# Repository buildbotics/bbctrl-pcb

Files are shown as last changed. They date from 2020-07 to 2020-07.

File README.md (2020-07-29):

# Buildbotics Controller Schematics & PCB Layout
The top-level schematic is in the file ``buildbotics_controller.sch``.  To view
and edit the schematics run:

    make schematics

You must have ``make`` and the GEDA tools install.  Other make commands are:

  * ``pcb``    - Open the PCB editor.
  * ``bom``    - Create Bill of Materials as ``buildbotics_controller.bom``.
  * ``net``    - Generate the netlist as ``buildbotics_controller.net``.
  * ``drc``    - Run the Design Rule Checker.
  * ``layout`` - Initialize the PCB layout.
  * ``attrib`` - Edit schematic part attributes.
  * ``zip``    - Create a zip file from the Gerber and drill files.
  * ``tidy``   - Remove all backup files.
  * ``clean``  - Remove all autogenerated files.

# Configuration notes
Copy the system gnetlistrc file:

    mkdir -p ~/.gEDA
    cp /etc/gEDA/system-gnetlistrc ~/.gEDA/gnetlistrc

Edit ``~/.gEDA/gnetlistrc`` and comment out (insert semicolon) the line that
reads:

    (hierarchy-netattrib-mangle "enabled")

and uncomment the line that reads:

    ;(hierarchy-netattrib-mangle "disabled")

The resulting lines should look like this:

    ;(hierarchy-netattrib-mangle "enabled")
    (hierarchy-netattrib-mangle "disabled")

This allows power and ground rails to be routed between schematics without
mangling the names.  Note, that as a consequence of this setting you cannot
use ``net`` attributes in any schematic modules that are used more than once
with out having them all connected together.

Set the library path in PCB to point to the local footprints folder.  Use
``File->Preferences->Library`` in PCB to do this.

# License
Copyright Buildbotics LLC 2016-2020.

This source describes Open Hardware and is licensed under the CERN-OHL-S v2

You may redistribute and modify this documentation and make products
using it under the terms of the CERN-OHL-S v2 (https:/cern.ch/cern-ohl).
This documentation is distributed WITHOUT ANY EXPRESS OR IMPLIED
WARRANTY, INCLUDING OF MERCHANTABILITY, SATISFACTORY QUALITY
AND FITNESS FOR A PARTICULAR PURPOSE. Please see the CERN-OHL-S v2
for applicable conditions.

Source location: https://github.com/buildbotics

As per CERN-OHL-S v2 section 4, should You produce hardware based on
these sources, You must maintain the Source Location clearly visible on
the external case of the CNC Controller or other product you make using
this documentation.

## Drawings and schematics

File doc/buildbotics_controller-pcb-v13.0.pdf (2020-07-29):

## buildbotics_controller.pcb

## 1. Table of Contents (This Page) Created on Wed Jul 29 16:05:18 2020 2. top 3. power 4. ground 5. bottom 6. plated-drill 7. unplated-drill 8. componentmask 9. soldermask 10. topsilk 11. bottomsilk 12. toppaste 13. topassembly 14. bottomassembly 15. fab

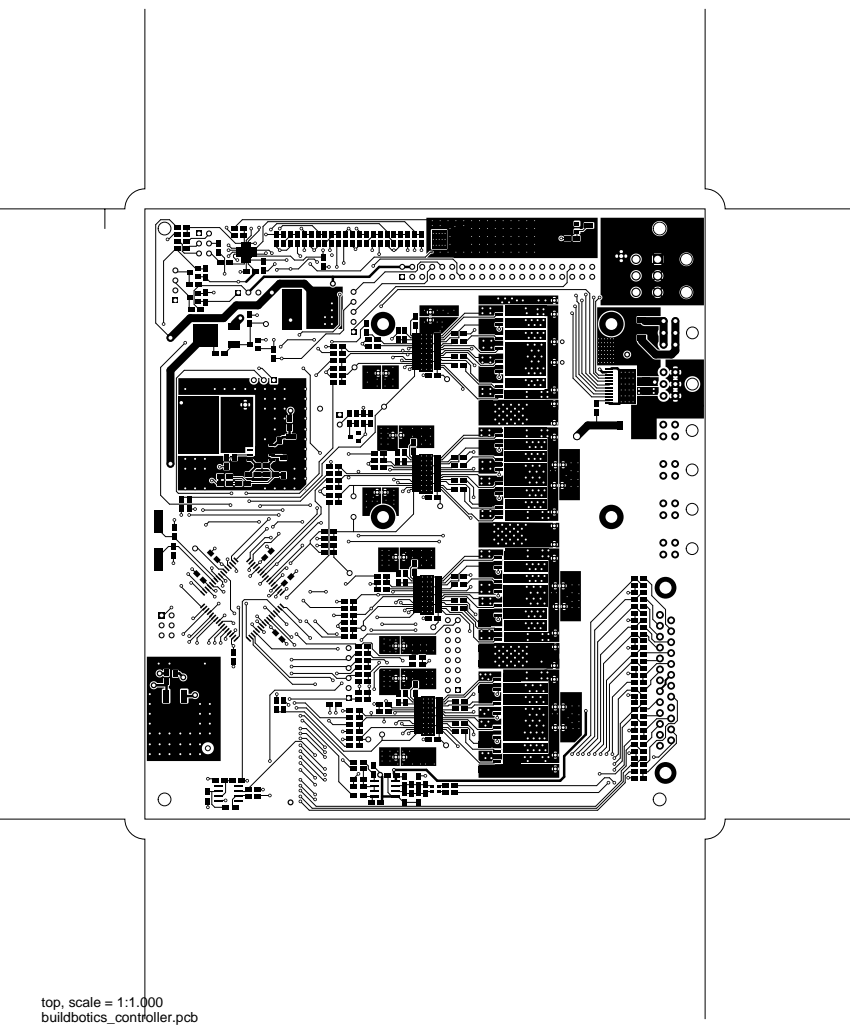
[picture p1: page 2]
top, scale = 1:1.000

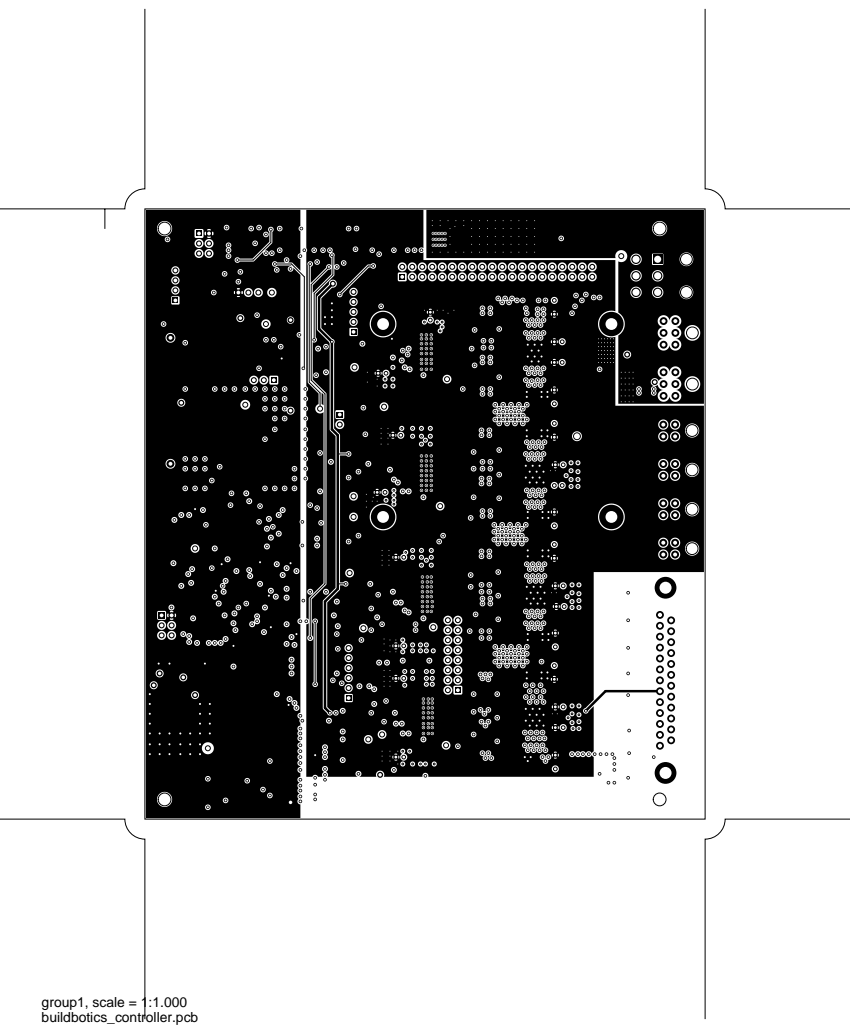
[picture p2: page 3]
group1, scale = 1:1.000

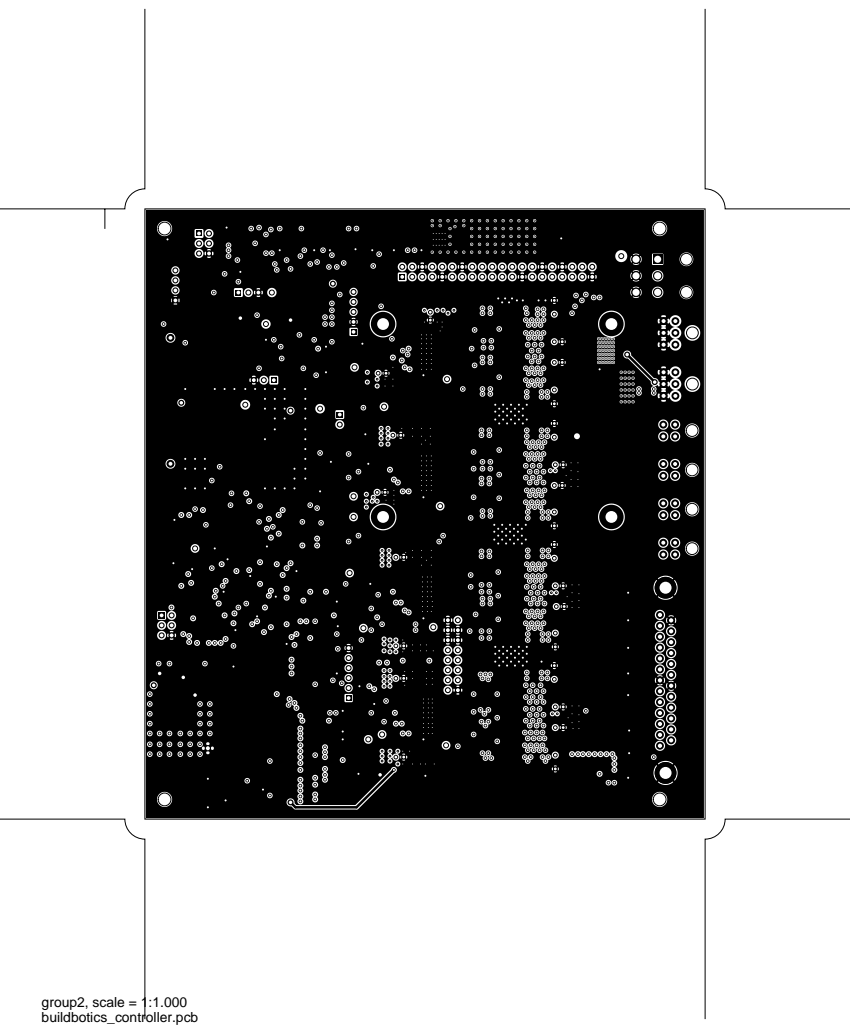
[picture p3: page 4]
group2, scale = 1:1.000

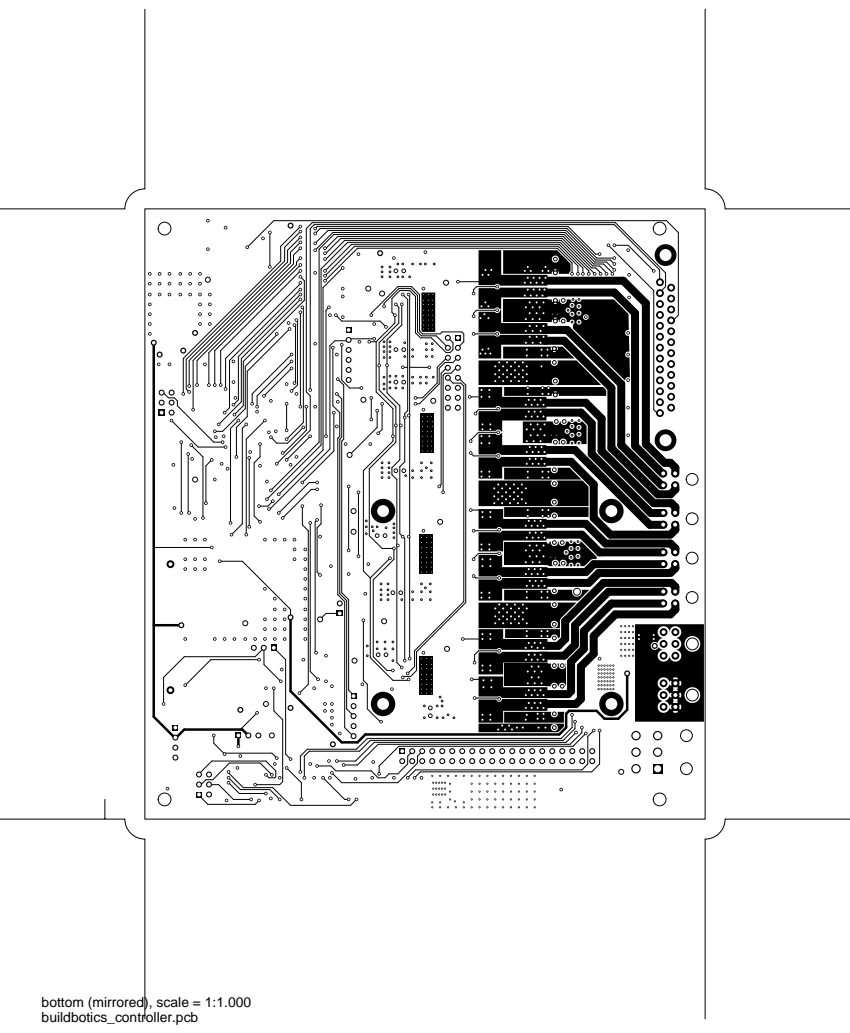
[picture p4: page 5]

bottom (mirrored), scale = 1:1.000

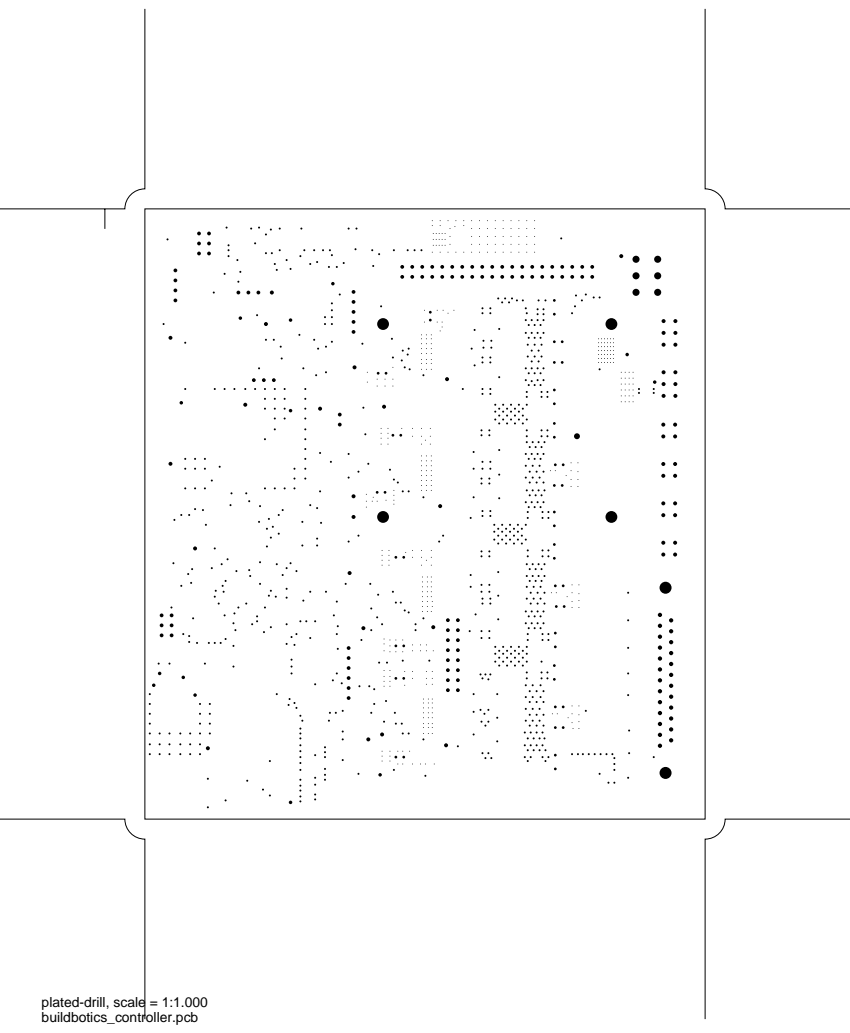
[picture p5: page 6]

plated-drill, scale = 1:1.000

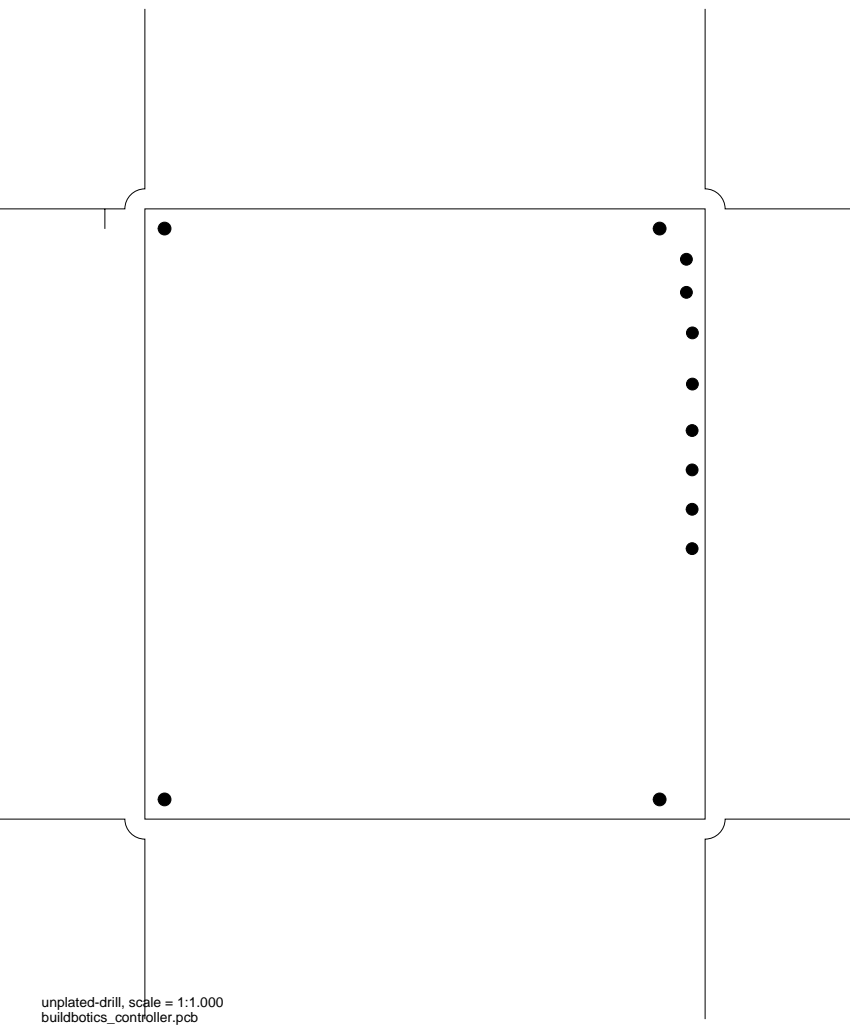
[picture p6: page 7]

unplated-drill, scale = 1:1.000

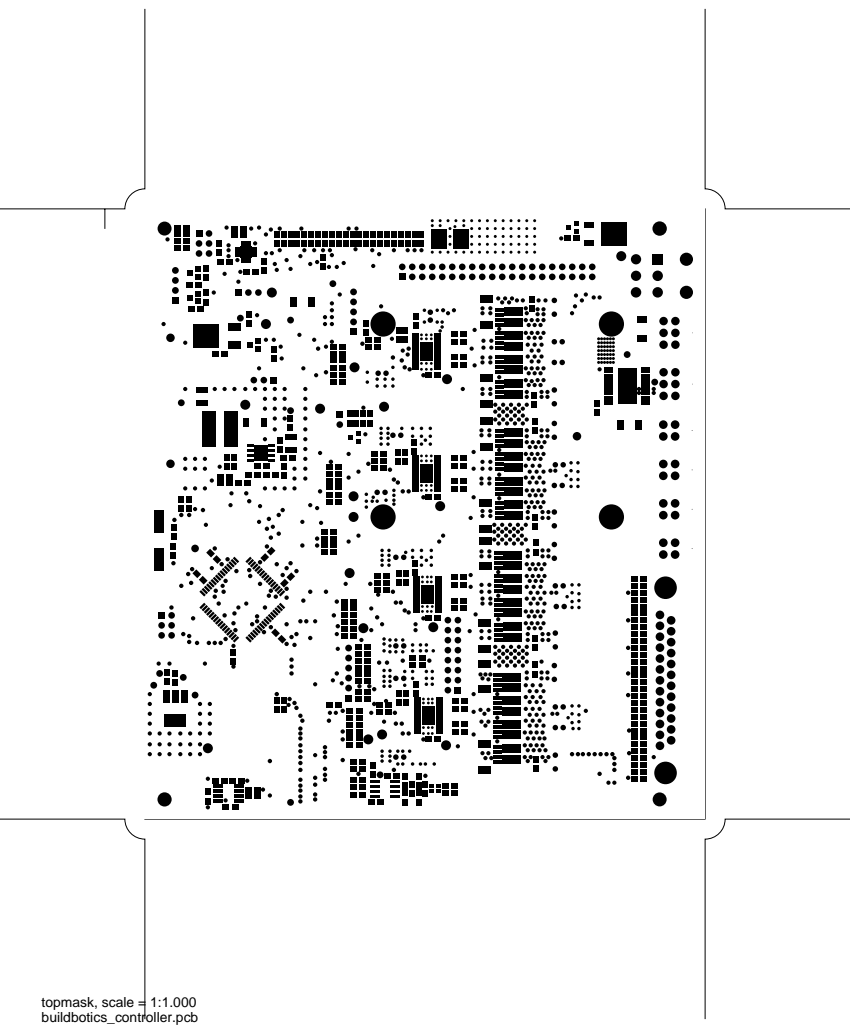
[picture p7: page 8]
topmask, scale = 1:1.000

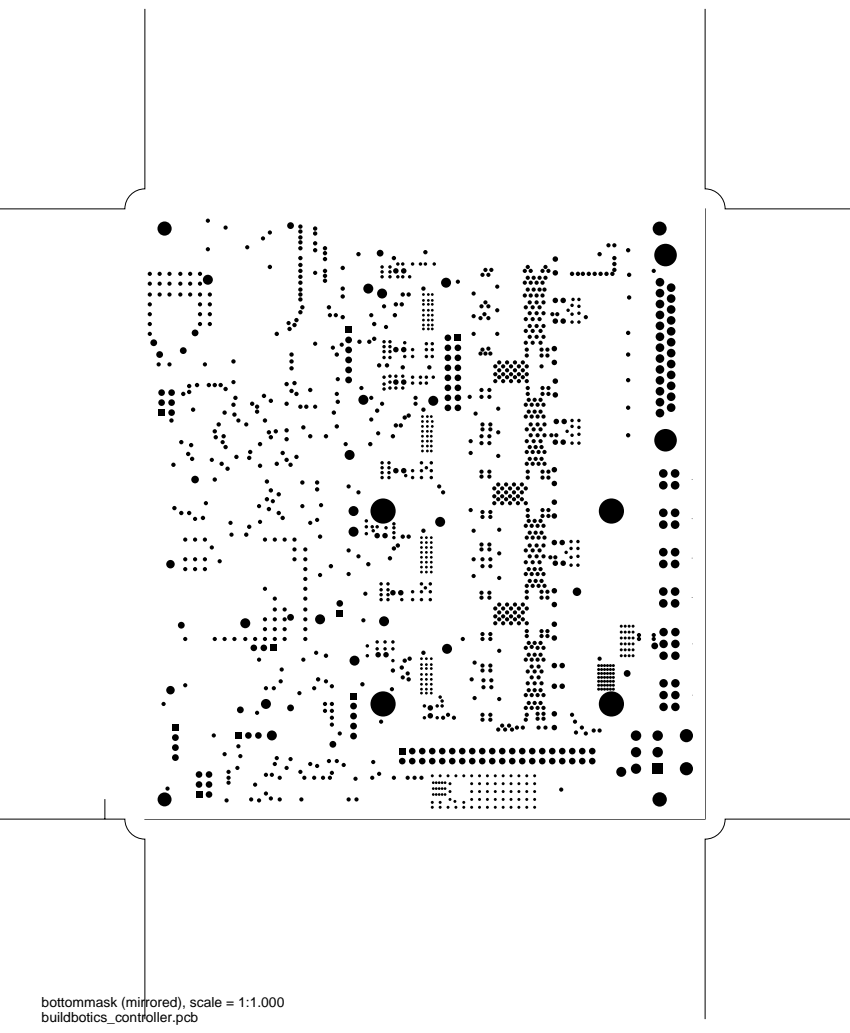
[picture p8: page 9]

bottommask (mirrored), scale = 1:1.000

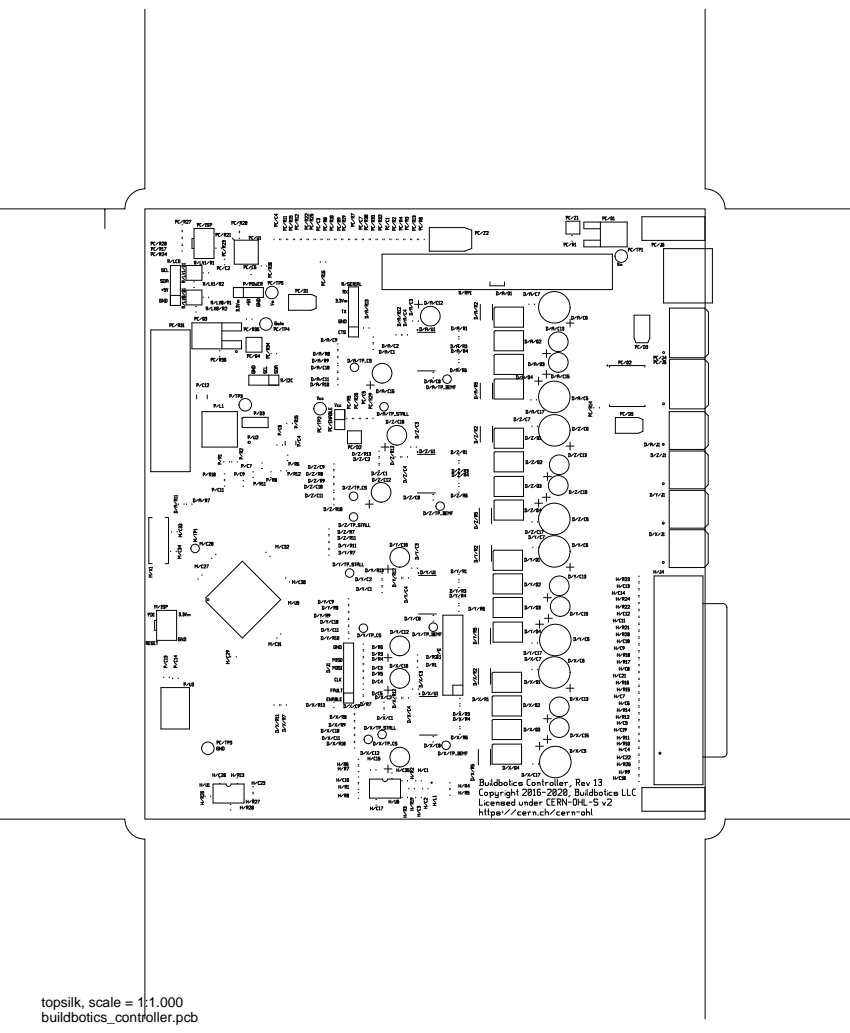
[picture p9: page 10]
topsilk, scale = 1:1.000

bottomsilk (mirrored), scale = 1:1.000

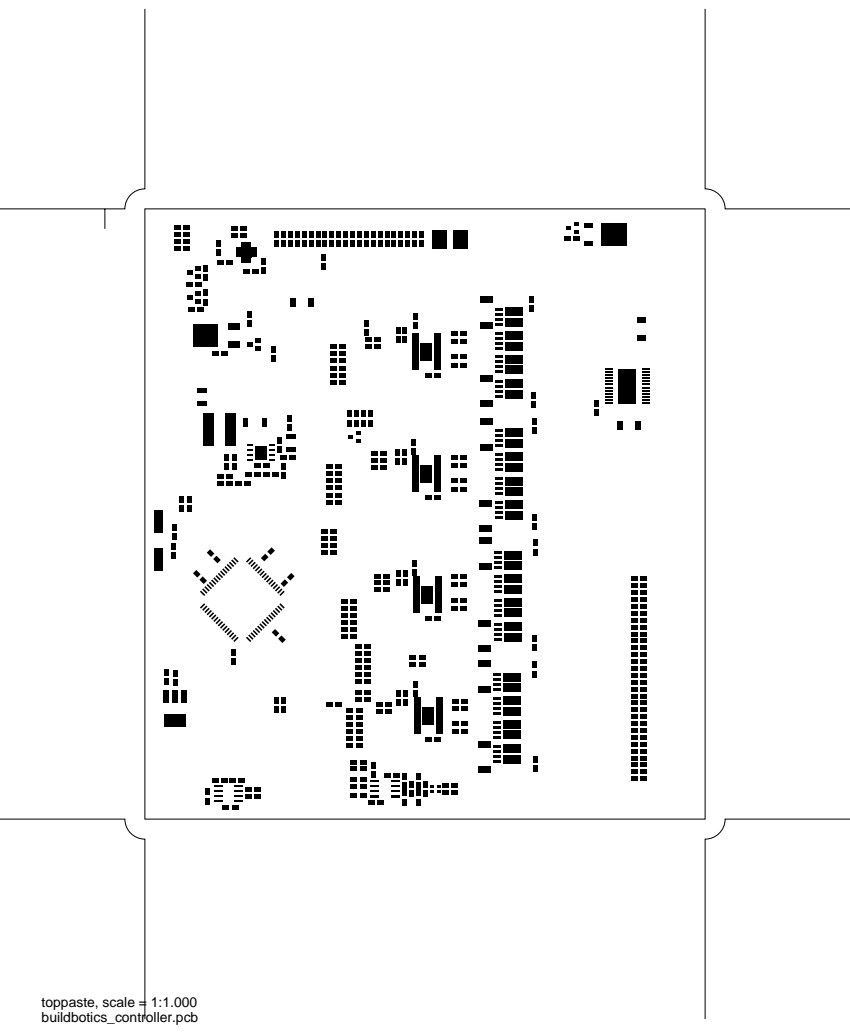
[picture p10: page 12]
toppaste, scale = 1:1.000

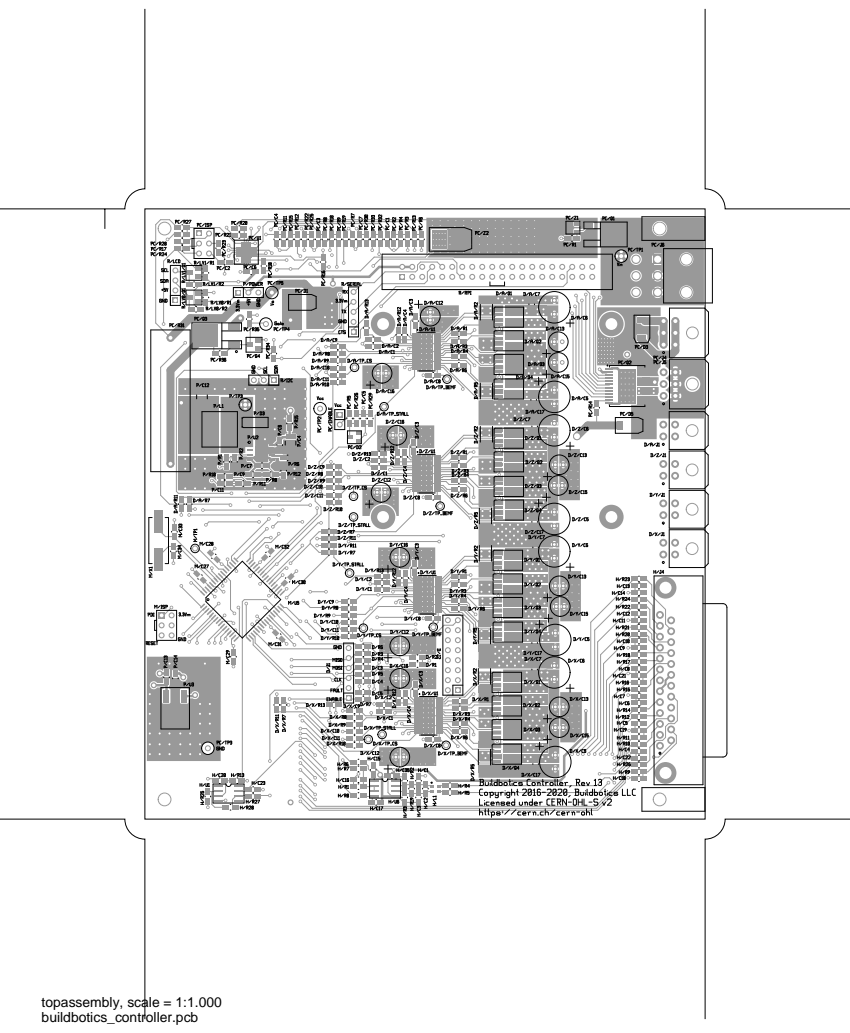
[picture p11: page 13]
topassembly, scale = 1:1.000

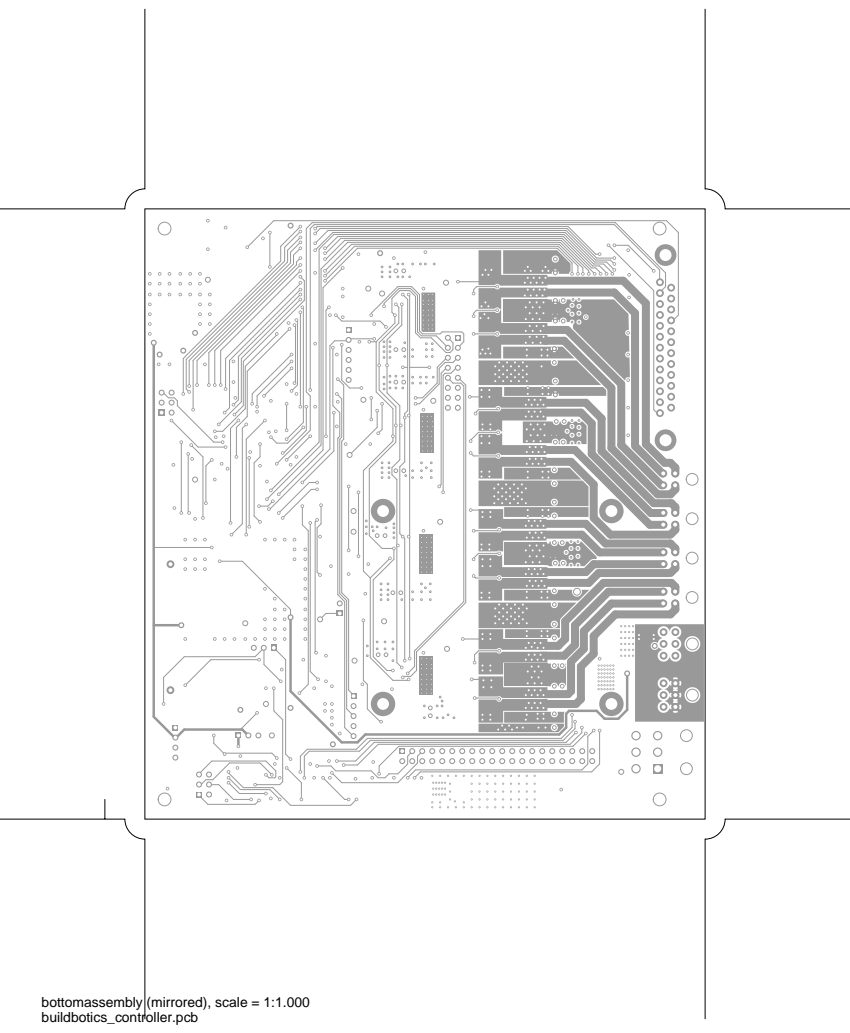
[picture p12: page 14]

bottomassembly (mirrored), scale = 1:1.000

fab, scale = 1:1.000

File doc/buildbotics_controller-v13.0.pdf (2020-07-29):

PAGE; DRAWN BY:

Level Converter
Copyright (c) 2016−2020, Buildbotics LLC
Licensed under CERN−OHL−S v2

Doug & Joe Coffland


NC NCMicroprocessor Copyright (c) 2016−2020, Buildbotics LLC

Licensed under CERN−OHL−S v2


Peripherals
Copyright (c) 2016−2020, Buildbotics LLC
Licensed under CERN−OHL−S v2


2 G1 | | | D1 | 7
3 S2 | D2 | 6
4 G2 | | | D2 | 5

Motor Driver
Copyright (c) 2016−2020, Buildbotics LLC
Licensed under CERN−OHL−S v2

PAGE; DRAWN BY:; Raspberry PI

Stepper Motor Drivers

Buildbotics Controller
Copyright (c) 2016−2020, Buildbotics LLC
Licensed under CERN−OHL−S v2

Doug & Joe Coffland


Power
Copyright (c) 2016−2020, Buildbotics LLC
Licensed under CERN−OHL−S v2

PAGE; DRAWN BY:

NC NC NC NC NC NC serial_tx:1 serial_rx:1 serial_cts:1

RPI Bus
Copyright (c) 2016−2020, Buildbotics LLC
Licensed under CERN−OHL−S v2

Doug & Joe Coffland


Power Conditioning
Copyright (c) 2016-2020, Buildbotics LLC
Licensed under CERN-OHL-S v2


Motor Modules
Copyright (c) 2016−2020, Buildbotics LLC
Licensed under CERN−OHL−S v2

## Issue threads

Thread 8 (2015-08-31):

Supply motor logic from motor driver 5-volt supply

DougCoffland, 2015-08-31:
a. We could avoid the second IRM-10-5 by using the 5v supply on the
TMC2660.  These could all just be ganged together.  Saves ~$7.50.

DougCoffland, 2018-02-13:
No longer desired.

Closed 2018-02-13.

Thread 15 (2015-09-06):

Consider copper filling/pouring in the ground plane

jcoffland, 2015-09-06:
Isn't it generally a good idea to copper fill the ground plane?  You've done this already for the motor ground but why not also do so for the logic ground plane?  I was able to do this by drawing a few polygons on layer `inner 2` so that they did not overlap the motor ground plane.  I didn't check this in though.  What do you think?

sntanala, 2019-06-09:
Hi jcoffland, my name is Satya, I am a learner and programmer for cnc controller, can you please let us know how can i open eagle schematics of this project, I tried all versions of eagle but we are getting error while open. can you please suggest me how to open these schematics to learn control flows.

Closed 2019-06-09.

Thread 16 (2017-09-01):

Schematic PDF

DirtyEngineer, 2017-09-01:
Including a PDF of the schematic would be great.

jcoffland, 2017-09-01:
Good idea: https://github.com/buildbotics/bbctrl-pcb/blob/master/doc/buildbotics_controller-v8.1.pdf

Closed 2017-09-01.

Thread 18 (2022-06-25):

Can we get a Kikad version of this?

ArcAIN6, 2022-06-25:
I was wondering if there were alternative formats for these schematics / PCB files? gEDA seems to be very antiquated, and not windows friendly at all. As i don't have a linux machine here, i tried to open these on raspberry pi, following the install directions on teh gEDA website, but the schematics won't show up, and the PCB viewer is  completely non-functional.

Any help would be great, as i'm interested in how these boards work

leventelist, 2023-11-01:
Yes please.

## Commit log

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2015-08-05 Reworked power, cleaned up symbols
    [connectors.sch, io_board.sch, io_bus.sch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]
2015-08-06 made schematic changes, started a new static file, added flag symbol, and added datasheet for nucleo
    [PowerSTEP01 board2.sch]
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2015-08-11 replacediodes on board because part is not available. New diodes are CDBU0130L
    [BOM.ods, PowerSTEP01 board.sch, PowerSTEP01 board2.sch]
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2015-08-12 corrected a few parts and created bill of materials (BOM.ods)
    [BOM.ods, PowerSTEP01 board.sch, PowerSTEP01 board2.sch]
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2015-08-22 fixed clock lines by adding clock.sch schematic ad symbol and modified isolation.sch accordingly
    [BOM.ods, clock.sch, isolation.sch]
2015-08-25 completed combined board layout. Still have warnings and one being reported as not routing. Will continue to investigate
    [BOM.ods, isolation.sch, microprocessor.sch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]
2015-08-25 I fixed the warnings but there gpcb still reports that one rat is not routed, even though it is not apparent from looking at the board. I also cut the board down to it's final size which is 85mm x 22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
2015-08-26 All warnings anre now cleared and all rats have been routed. In addition, BOM has been created (see BOM.ods) and gerbers are presnt
    [BOM.ods, motor_driver.sch, rpi_bus.sch]
2015-08-29 This is a major rework. I changed board size to 5 X 8 inches and 4 layers. I also added the 26-Pin DSub connector for the IO connector. I also reduced the number of drivers to four. I added mounting 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
    [BOM.ods, clock.sch, combined.sch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]
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2015-08-30 Corrected some errors so it now passes BayArea Circuits DFM tool and corrected a bunch of local DRC errors. Still working on correcting DRC errors.
2015-08-30 corrected hole size for 26 pin dsub foot print and corrected all DRC errors below 6 mils
2015-08-30 Corrected foot print for 260 mil cap and 8 by 10 cap - All DRC errors below 7.5 mils are now correct. Still get a warning however that a hole is too close to a line.
2015-08-30 corrected footprint for 2-pin Molex. All DRC below 7.5mil corrected and no warning about hole too close to line.
2015-08-31 All DRC errors cleared. No errors or warnings using Advanced Circuits FreeDFM tool.
    [microprocessor.sch, motor_driver.sch]
2015-08-31 dir_4 and step_4 were swapped on the schematic and therefore swapped ont the layout. The schematic and layout have been corrected.
    [motor_module.sch]
2015-09-01 Corrected pin swap of serial_rx and serial_tx and fixed missing refdes on RPI connector
    [combined.sch, microprocessor.sch, rpi_bus.sch]
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2015-09-03 New board with corrected connectors, removal of extra IRM-10-5, replacement of digital isolators withoptos, etc... No DRC errors, not errors or warnings at Advanced Circuits DFM. This board is marked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
    [BOM.ods, clock.sch, isolation.sch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]
2015-09-04 moved clock oscillator on board reducing total clock line length from 8 inches to 3 inches
2015-09-04 cleared all DFM errors and created BOM
2015-09-05 corrected footprint size for PS1/C1
    [power.sch]
2015-09-05 corrected raspberry pi connector and board footprint, added outline to layout, corrected footprint on PS1/C1, started working on final BOM file
    [BOM.ods, rpi_bus.sch]
2015-09-05 corrected soldermask line width around raspberry_pi mounting holes
2015-09-06 scrubbed BOM and created ASSY_BOM.xlsx for assy estimate, corrected footprint for PS1/C4, made land pattern for OSC match datasheet land pattern, assigned part numbers to MP1/C2 and C3 and corrected 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
    [BOM.ods, microprocessor.sch, power.sch]
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2015-09-06 corrected land pattern for C17 on the Motor Drivers
2015-09-06 Corrected connection to 5VOUT on motor drivers, updated layout, expanded ground plane on layout
    [motor_driver.sch]
2015-09-06 io labels in microprocessor.sch corrected
    [microprocessor.sch]
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2015-09-08 corrected pin order on PS1/J2 footprint and then fixed layout accordingly
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2015-09-10 replaced 0201 caps on microprocessor.sch with 0402s to lower assembly cost; affected combined.pcb, BOM.pcb, and ASSY_BOM.xlsx
    [BOM.ods, microprocessor.sch]
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2015-09-11 reviewed and verified all footprints, updated BOMs with new io connecton for e-stop, updated rpi_bus.sch with new connector circuit for e-stop, created BOMs and centroid files for thru hole and no th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
    [BOM.ods, rpi_bus.sch]
2015-09-27 added tabs to RPI/J1 and RPI/J2; confirmed no DFM errors on Advanced Circuits DFM tool
    [rpi_bus.sch]
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2015-11-30 added files describing back, bottom, and top of enclosure, and added logo file
    [backview.dxf, bottomplate.dxf, topcover.dxf]
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2016-02-04 Fixed net attributes
    [microprocessor.sch, motor_driver.sch, motor_module.sch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]
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2016-02-05 Fixed DRC errors
    [microprocessor.sch, motor_driver.sch, rpi_bus.sch]
2016-02-05 Shortened refdes, make changes, docs
    [buildbotics_controller.sch, motor_module.sch]
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2016-02-08 v2.0 close to done, finalized connectors, add some footprints, removed unused footprints
    [buildbotics_controller.sch, load.sch, microprocessor.sch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]
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2016-02-09 Fixed LED
    [peripherals.sch]
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2016-02-09 fixed name of kingbright footprint file
2016-02-09 fixed kingbright footprint again
2016-02-09 changed Power Supply J1 from 350944 (which is male) to 643230 (which is female) which now mates correctly with the male connector on the mean well GS280 power supply. Created footprint for 643230. Re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
    [power.sch]
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2016-02-10 fixed pin numbers on mosfet symboll for load/Q2
    [load.sch]
2016-02-10 fixed rpi footprint and added board outline to footprint. Updated rpi_bus.sch with correct footprint
    [rpi_bus.sch]
2016-02-11 corrected spelling on footprint name for LM5160
    [power.sch]
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2016-02-11 modified power.sch to make switch S1 into two tabs, assigned device Keystone 1212 to use a through hole tab, and made footprint for Keystone 1212 tab.
    [power.sch]
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2016-02-12 added part numbers for R11, R13, C23, C24 in motor_driver.sch. Added C25 and C26 across sense resistors as per section 8.1 of tms2660 datasheet.Continued to update layout in buildbotocs_controller.pcb
    [motor_driver.sch]
2016-02-12 fixed 3.3V_motor.sym to use net=3.3Vm:1 instead of net=+5Vm:1. Continued with layout and continued updating motor_driver.sch to reflect component model names
    [motor_driver.sch]
2016-02-15 continued to work on layout updating buildotics_controller.pcb; continued to identify specific parts in schematic and added part numbers and descriptions in load.sch, motor_driver.sch, peripherals.sc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
    [load.sch, motor_driver.sch, peripherals.sch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]
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2016-02-16 corrected value for P/C4 from 4.7uF to .47uF per 8.1.2.1.7 in the LM5160 datasheet, completed assigning part numbers in power.sch and motor_driver.sch; continued layout work
    [motor_driver.sch, power.sch]
2016-02-16 fixed footprint for LM5160 (no pin numbers were assigned; continued layout
    [power.sch]
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2016-02-18 PCB layout complete with no local DRC errors
    [rpi_bus.sch]
2016-02-18 fixed footprints to increase clearance to make DRC pass
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2016-02-19 layout complete, no DRC errors, Cleared all show stoppers from FreeDFM; Cleared many warnings from FreeDFM ( had to increase soldermask size on most of the footprints that I created. Reduced board wo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
    [microprocessor.sch]
2016-02-19 board layout complete with no local DRC errors and no errors or warnings from freeDFM. Note, also deleted unused raspberry_pi_board.fp footprint file
2016-02-20 assigned specific part numbers and values to each component in the schematics
    [load.sch, microprocessor.sch, motor_driver.sch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]
2016-02-20 started BOM; continued to specify exact part numbers in schematics; extended footprint on MAX14850 as requested by Mike; updated pcb layout accordingly
    [BBC_BOM.ods, motor_module.sch, power.sch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]
2016-02-20 completed bill of materials; changed ISP connector from right angle to vertical; added value field to some parts to make compatible with bill of materials output
    [BBC_BOM.ods, load.sch, microprocessor.sch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]
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2016-02-21 changed sense resistors from 1206s to 2512s; updated schematic,BOM, centroid file, and layout accordingly
    [motor_driver.sch]
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2016-02-26 Added reverse voltage protection
    [power.sch]
2016-02-28 changed board size to 152.3mm x 142.3mm and re-centered layout; Added mounting holes; removed R/LED1, R/R22, and R/R23; replaced fuse/diode polarity protection circuit with NMOSFET/diode/resistor pro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
    [power.sch]
2016-02-29 added footprint file for 2512 resistors, replaced P/D1 with part recommended by Joe, completed layout with no shorts, DRC errors, or FreeDFM errors
    [power.sch]
2016-02-29 Schematic cosmetic updates, changed LD#/J1 pinout, Fixed disconnect on rpi_sda
    [load.sch, power.sch, rpi_bus.sch]
2016-03-01 implemented all of Joes recommendations; NDRC errors; fully routed; added copyright, board name; and company name to silk screen
    [microprocessor.sch]
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2016-03-08 updated supporting parts list and made dxf files for front and back panel of enclosure
    [back_panel.dxf, front_panel.dxf]
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2016-06-03 Attempts to fix LM5160 circuit
    [load.sch, microprocessor.sch, peripherals.sch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]
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2016-06-15 added 1210 footprint with extended pads, referenced 1212_ext in power.sch, referenced 0805_ext in level_converter.sch
    [level_converter.sch, power.sch]
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2016-06-17 Rearranged AVR & DB25 pins, Moved reset line on isolator, Added grounds to motor test headers
    [microprocessor.sch, motor_driver.sch, peripherals.sch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]
2016-06-19 created footprints for C10, T1, Z2, and D2 in power.sch and referenced all parts in Isolated Flyback circuit schematic to models and footprints
    [power.sch]
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2016-06-19 changed 0805 footprints in load.sch to 0805_ext, created footprint for common mode choke in peripherals.sch and updated footprints and footprint references in peripherals.sch.
    [load.sch, peripherals.sch]
2016-06-19 corrected references to pin 2 in 0806_ext.fp and DO214AC.fp, fixed mounting hole in Molex_39-30---6-.fp, made mounting holes metal connection to pin 26 in NORCOMP_182-025-113R151_DB25M.fp, corrected 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
    [power.sch]
2016-06-20 corrected wiring on P/J1, fixed wiring on motor connectors, connected P/R1 to pwr_en so Vs is off when the switch is off
    [motor_driver.sch, power.sch]
2016-06-23 completed layout with no DRC, no shorts, and all nets routed, still need to submit to Advanced Circuits for DFM check, increased clearance on SRF2012A footprint, added new schottkyA2K1.sym symbol due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
    [load.sch]
2016-06-23 changed zener symbol to match footprint and updated power.sch, note this was done before the previous push but I for did not get these files included. Current status is layout is done, but still need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
    [power.sch]
2016-06-24 adjusted clearance on SRF2012A footprint, all DFM errors now cleared with Advanced Circuits
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2016-06-26 modified softstart circuit in power.sch, removed Zener in polarity control circuit, changed R20 to 100 ohms decreasing C1 charge time, reduced C20 to 1uF reducing Q1 turnon time, added D4 to provide 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
    [power.sch]
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2016-06-26 Fixed zener alignment, added new poposed power conditioning circuit.
    [power2.sch]
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2016-06-29 Fixed schematic DRC warings/errors, added caps to H/J4 input lines, Renamed peripherial module P->H to avoid conflicts with RPI module
    [buildbotics_controller.sch, peripherals.sch, power.sch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]
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2016-06-30 layout complete, not opens, shorts, DRC errors,or DFM errors. Changed Diode D1 in power.sch to get smaller footprint.
    [power.sch]
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2016-07-01 cleared all dfm errors and moved silkscreen labels around
2016-07-02 changed some part numbers because we were using different models for exactly the same part. This allows us to get larger volumes and fewer different parts
    [motor_driver.sch, peripherals.sch, power.sch]
2016-07-03 fixed a DRC error and corrected board width to 142.3mm
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2016-07-26 Added i2c bus from RPi to AVR, fixed some part numbers
    [microprocessor.sch, motor_driver.sch, peripherals.sch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]
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2016-07-28 Fixed PCB schematic path, Fixed bad MOSFET pin numbers
    [level_converter.sch, load.sch, power.sch]
2016-07-29 layout done, DRC and DFM errors cleared, fixed footprint for P/U5 because footprint did not match symbol, reversed power rails in P/U5 because the appeared to be connected backwards, changed foorprin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
    [power.sch]
2016-08-05 Check all PCB major parts, improved routing, fixed MOSFETs
    [level_converter.sch, load.sch, microprocessor.sch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]
2016-08-16 Split RPi footprint, Moved RPi mounting holes, Better noise immunity, Routing improvements.
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2016-08-18 fixed soldermask clearance on seveal vias
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2016-09-29 Fixed cap value
    [power.sch]
2016-10-09 Replaced TMC2660 with DRV8711, Added filtering to serial lines, Modified motor connector footprint pin numbers, Connected BEMF lines to AVR
    [microprocessor.sch, motor_driver.sch, motor_module.sch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]
2016-10-09 Added correct refdes to resistors
    [motor_module.sch, rpi_bus.sch]
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2016-10-09 Fixed schematic DRC violations
    [motor_driver.sch, rpi_bus.sch]
2016-10-10 added model numbers to C1 an C2 in rpi_bus.sch. The are caps that Joe added to the serial lines.
    [rpi_bus.sch]
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2016-10-10 replaced power conditioning circuit in power.schj
    [power.sch]
2016-10-10 corrected conflicting refdes's in power.sch
    [power.sch]
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2016-10-10 assigned component model numbers and descriptions as needed in motor_driver.sch and motor_module.sch
    [motor_driver.sch, motor_module.sch]
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2016-10-10 created footprint for DRV8711, added footprints for Nichicon 3mm cap and TO252. Updated references to new footprints in schematics. All footprints now load into pcb and I can start routing
    [motor_driver.sch, power.sch]
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2016-10-13 Fixed motor driver connections, shunk power supply symbols.
    [microprocessor.sch, motor_driver.sch, motor_module.sch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]
2016-10-14 Layout complete, no shorts, no opens, noDRC errors, no DFM errors from Advanced Circuits. Includes new L7986A layout and new place for 3-pin header for enable switch connection and new power supply c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
    [power.sch]
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2016-10-16 Added new power conditioning circuit, some PCB fixes
    [power.sch]
2016-10-16 assigned correct footprint to LM293DT in power.sch
    [power.sch]
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2016-10-19 assigned part numbers to power.sch, finished layout in buildbotics_controller.pcb, put in new power circuit, moved +5 iso, +5Vm, and +3.3Vm powersupplies around for better routing, moved digital isol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
    [power.sch]
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2016-10-20 new schematic reflects new dual mosfets with drain tabs, corrected routing of ASENSE test point line, it was going to the wrong place
    [motor_driver.sch]
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2016-10-21 Fixed cap values
    [peripherals.sch]
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2016-10-24 layout complete with no legitimate DRC errors, removed filter components on open collector lines in schematics, corrected connection of senseA lines in drivers
    [load.sch, motor_driver.sch, motor_module.sch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]
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2016-10-30 replaced power supply filter caps in motor_driver.sch with modeled components and added footprint files as needed
    [motor_driver.sch]
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2016-10-30 removed unnecessary resistors in gate drive lines in motor_driver.sch and in layout
    [motor_driver.sch]
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2016-10-31 replaced caps with values that Joe and I agreed upon
    [motor_driver.sch]
2016-10-31 removed and replaced caps on schematic and layout and added footprint for one electolytic"
    [motor_driver.sch]
2016-11-02 layout complete with no legitimate DRC errors, changed testpoints a bit in power.sch and rpi_bus.sch to make routing easier
    [power.sch, rpi_bus.sch]
2016-11-03 added capacitance pours to bottom layer, all DRC and DFM errors cleared
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2016-11-05 Moved all unlocked parts, lines and vias on to grid. Fixed via thermals. Lots of fixes to silk layer. Moved level shifters. Moved power cond. circuit. Added missing labels. Fixed R/SERIAL labels. Ali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
2016-11-05 Fixed connector positions and locked them
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2016-11-07 Increased clearance and thermal finger width
2016-11-12 corrected some part numbers
    [motor_driver.sch, power.sch]
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2016-11-23 fixed footprint for P/J1, improved footprint fo TSSOP38 by reducing solder mask clearance, moved non-ISO PS up, level shifters down, and power conditioning compomponents down a little to allow slidin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
    [power.sch]
2016-11-25 changed a couple of part numbers for equal valued comcomponents so we could get larger quantities of individual part numbers
    [level_converter.sch, power.sch]
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2017-01-04 fixed solder mask violations
2017-01-06 power_cond.sch and .pcb updated, mask clearance corrected in footprint file
    [power_cond.sch]
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2017-02-23 Fix grid alignment, moved power_cond3 -> power_cond
    [power_cond.sch, power_cond3.sch]
2017-02-26 latest power_cond sicruit with self protecting fet, also includes load circuit switches for testing
    [power_cond.sch]
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2017-02-27 corrected footprint for ATiny, started power_cond.pcb layout, corrected symbol for ATiny, added decoupling cap on ATiny in power_cond.sch and reconnected pin21 to gnd.
    [power_cond.sch]
2017-02-28 Power cond fixes & cleanup
    [power_cond.sch]
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2017-02-28 corrected footprint attribute for ISP and J3 in power_cond.sch, corrected footprint for ATiny, completed layout in power_cond.pcb
    [power_cond.sch]
2017-03-03 added diodes on outputs and added reverse battery battery circuit in parallel with zero ohm resistor in power_cond
    [power_cond.sch]
2017-03-07 created power_conditioner.sch (and a symbol) from power_coind.sch and incorporated the result into power.sch. Also, changed C2 to .22uF 100V from 0.1uF 50V in motor_driver.sch and added resistors int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
    [motor_driver.sch, peripherals.sch, power.sch]
2017-03-08 corrected PGND in power_conditioner.sch and updated layout
    [power_conditioner.sch]
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2017-03-19 corrected enable circuit in power.sch to ensure that ISO 5V is off when enable is off
    [power.sch]
2017-03-21 PCB fixes, removed 3.3v linear regulator, buck to 3.3v directly, updated copyright, added zero ohm resistors to isolate subcircuts.
    [buildbotics_controller.sch, level_converter.sch, load.sch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]
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2017-05-30 Changed power such that second fet on smart fet is enabled through enable switch and delayed turnon. When second fet comes on, power is applied to the attiny and the 5V iso and 3.3Vm power supplies. 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
    [motor_driver.sch, power.sch, power_conditioner.sch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]
2017-06-05 made corrections to part names so the BOM files build correctly, replace P/D3 model from V15P45-M3/86S to STPS3L40UF. V15P45 not available and STPS3L40UF is what is used in the demo board for the L79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
    [microprocessor.sch, motor_driver.sch, power.sch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]
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2017-06-14 Fixed layer colors, Removed outline layer, Routed new analog_2 signal, Added two new guide holes
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2017-06-16 Increased trace size on 3.3V line from RPI, Moved r/LV1/R1 slightly to the right to improve clearance, Moved vias and one component away from the edge of the board to avoid conflict with enclosure
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2017-06-29 Moved Vout pwr input to PA7 to avoid problem with PC2
    [power_conditioner.sch]
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2017-07-01 corrected part number for R/U4
    [rpi_bus.sch]
2017-07-10 Fixed Pwr AVR power. Vdd -> v3.3m. Oops!
    [power_conditioner.sch]
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2017-10-21 Try powering DRV8711 logic, Replaced P/R2 with 1.37k 1% to make sure U2 turns at 12v, Finished removing iso, Added shunt circuit
    [buildbotics_controller.sch, motor_driver.sch, power.sch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]
2017-10-21 Fix rpi bus
    [rpi_bus.sch]
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2017-10-28 V9 board layout complete, no DRC or DFM errors. added footprints for new fets for clamping ciruit, changed motor_driver and rpi_bus schematics to have individual zero ohm resistors for each motor dri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
    [motor_driver.sch, power.sch, power_conditioner.sch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]
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2017-10-30 Fixed solder mask openings, silk overlaps, improved layout, moved Vs and Vcc test points.
2017-12-04 Moved Vcc test-point, Moved vias and power trace away from edge, Removed Do not populate from R/R15, Swapped RX/TX, Changed PC/R20 to 37.4 Ohm, Marked direction of ISP headers
    [level_converter.sch, microprocessor.sch, peripherals.sch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]
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2017-12-13 added solder mask clearance on vias under pad for P/Z2 to make FreeDFM happy
2017-12-13 changed H/R25 from 26.1 to 27 ohms because Elecrow could not source the 26.1 on the last batch.
    [peripherals.sch]
2018-01-16 Swapped load switch nets 1<->2
    [microprocessor.sch, peripherals.sch, power_cond.sch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]
2018-02-24 replaced PC/D1, PC/D3, and PC/D5 with new diode and updated footprint
    [power_conditioner.sch]
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2018-08-16 Added 0-10v circuit, changed low-pass filter values, rearranged motor step/dir headers, removed 3.3v output resistor, Changed 3.3v regulator, 5Ohm shunt, added missing cap on analog2
    [buildbotics_controller.sch, level_converter.sch, microprocessor.sch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]
2018-08-23 moved caps on input lines on DB25 connector to the other side of the resistor
    [peripherals.sch]
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2018-08-27 fixed solder mask clearances aroun vias
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2019-09-19 PCB/schematic corrections
    [power_conditioner.sch]
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2019-09-20 adjusted size of solder clearance on pads on P/u2 to pass freedfm, removed and added PC/R36 to get resistor value to take in the bom file
2019-09-29 Fixed two new DRC errors that showed up with PCB 4.2.0
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2020-08-07 removed resistors and caps, and added diodes on 3.3V inputs, added 3.3V to 5V level shifters on outputs, replaced level shifters on LCD interface
    [3.3V_to_5V_level_shifter.sch, motor_driver.sch, motor_module.sch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]
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2020-08-16 replaced Quadfet with LM5060 circuit
    [power.sch, power_conditioner.sch]
2020-08-17 added thermistor to prevent inrush on 5V power supply, noticed "ERROR WHILE CLIPPING PRO_SUB3" error
    [power.sch]
2020-08-19 made board with three options for charging caps at 5V power supply. Passed all DFM errors
    [peripherals.sch, power.sch, power_conditioner.sch]
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2020-08-26 fixed some part numbers and removed post script drawing of power conditioner circuit.
    [3.3V_to_5V_level_shifter.sch, peripherals.sch, power_conditioner.sch]
2020-08-28 corrected symbol name for PC/Q2
    [power_conditioner.sch]
2020-08-28 corrected symbol for p/q1 and updated pcb and schematic
    [power.sch, power_conditioner.sch]
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2020-09-23 corrected level shifters
    [3.3V_to_5V_level_shifter.sch]
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2020-09-23 fixed solder mask on a bunch of vias
2020-09-23 replaced 5V on H/J4 with spin0-10
    [peripherals.sch]
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2020-09-27 made corrections to reset:1 net
    [microprocessor.sch, rpi_bus.sch]
2020-10-12 Added routed missing PDI connection, Fixed text alignment and untangled some wires in schematic, Ran PCB clean up scripts, Move PCB silk elements away from vias, Removed unused symbol and footprint f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
    [3.3V_to_5V_level_shifter.sch, buildbotics_controller.sch, level_converter.sch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]
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2021-03-09 corrected enable circuit
    [power.sch, power_conditioner.sch]
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2021-04-05 replaced HV7802 with TSC2102 and replaced driver fets with part that is available, updated layout
    [motor_driver.sch, peripherals.sch, power.sch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]
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2021-04-08 Replaced some parts due to lack of RoHS documentation
    [buildbotics_controller.sch, microprocessor.sch, motor_driver.sch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]
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2022-02-09 moved voltage planes away from board edges. Replaced PC/C2 with 2.2uF ceramic. Moved drv_enable from AVR to ATTINY (makes it 5V signal), also added a 10K pull down to this line
    [microprocessor.sch, motor_module.sch, power_conditioner.sch]
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
